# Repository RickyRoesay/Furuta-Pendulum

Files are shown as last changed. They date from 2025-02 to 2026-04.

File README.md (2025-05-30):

# Furuta-Pendulum
Rotary Inverse Pendulum that acts like a cool desktop toy.  This project is a work in progress.
Inspired by [Ben Katz.](https://build-its-inprogress.blogspot.com/search/label/Pendulum)

**Goals:**  
  * Cheap to make.  That means no $100 encoders or outsourced manufacturing.
  * (Relatively) Easy to manufacture and assemble.  Only 3D printed parts and off the shelf components. No metalworking lathes.
  * Must have a screen and buttons for a selectable mode of operation (swing up, swing down, etc).  *It's not feature creep, I swear!*
  * LED's that track the position and angle of the pendulum.  *Totally not feature creep!*
  * Project timeline should be less than a year.  Must use/adapt pre-existing software and hardware when possible. 

&nbsp;

**Proof of concept:**



&nbsp;

**Photos of CAD Assembly:**

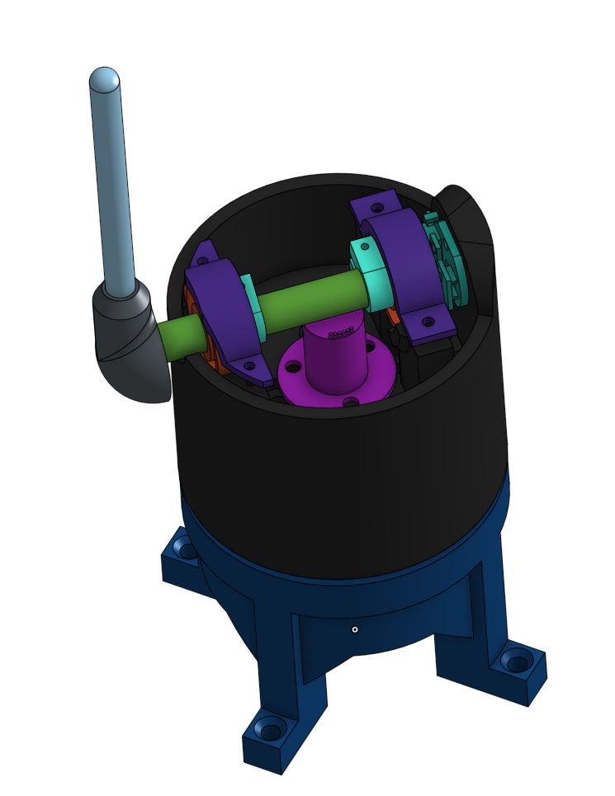
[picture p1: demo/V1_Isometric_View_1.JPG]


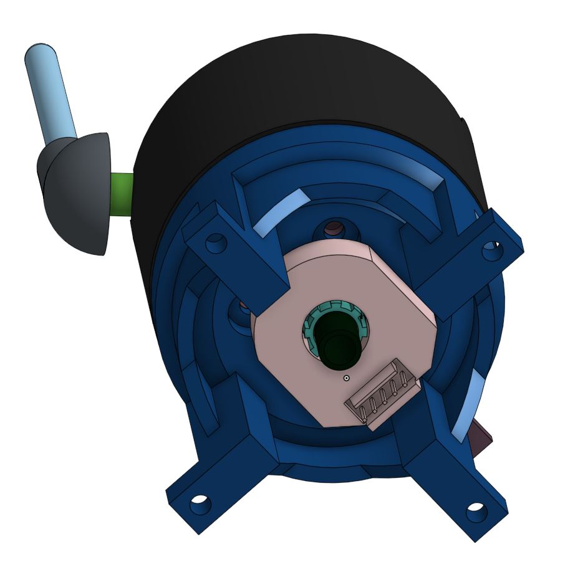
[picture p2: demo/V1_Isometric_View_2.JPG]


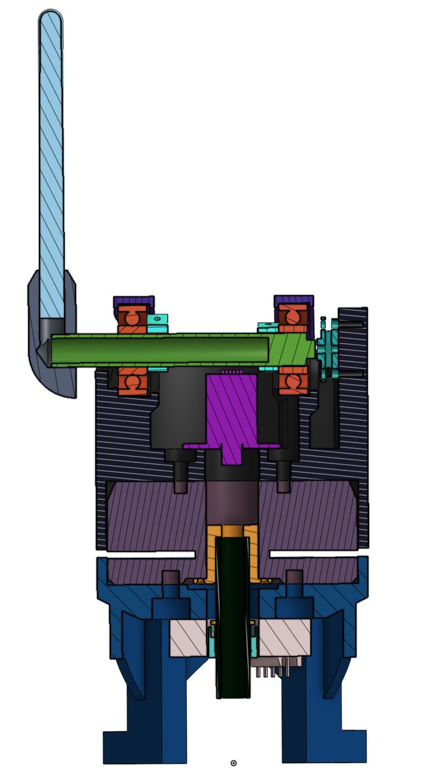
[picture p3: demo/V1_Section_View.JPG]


Link to the Onshape assembly can be found [here.](https://cad.onshape.com/documents/4a67b189595e38217c106822/w/59857a47126e04b0fa59ae61/e/db35a9295bf508af3468f325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)

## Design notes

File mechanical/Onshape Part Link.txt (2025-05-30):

https://cad.onshape.com/documents/4a67b189595e38217c106822/w/59857a47126e04b0fa59ae61/e/db35a9295bf508af3468f325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

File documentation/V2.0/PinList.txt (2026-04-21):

AS5047_nCS  -> PB2                  GPIO config'd, not a slave select pin
AS5047_CLK  -> Aux1 A -> PA5        AF5, SPI1 SCLK
AS5047_MISO -> Aux1 B -> PB4        AF5, SPI1 MISO
AS5047_MOSI -> Aux1 C -> PA7        AF5, SPI1 MOSI
SSD1357__D#                     -> Aux1 E -> PB3 & PB9
SSD1357__nRST                   -> Aux1 D -> PA15
SSD1357__SCLK                   -> Aux2 A -> PF1                       AF5, SPI2 SCLK
SSD1357__MISO                   -> Aux2 B -> PF0 & PA10 (PA10 used)    AF5, SPI2 MISO
SSD1357__MOSI                   -> Aux2 C -> PC4 & PA11 (PA11 used)    AF5, SPI2 MOSI
SSD1357__nCS                    -> Aux2 D -> PB7                       
SPI3_SCLK
SPI3_MOSI
SPI3_MISO
IMU_nCS
IMU_INT1
IMU_INT2
DRV8323_nCS
DRV8323_nFAULT
DRV8323_ENABLE
EEPROM_nCS
EEPROM_nWP
PH_A_HS
PH_A_LS
PH_B_HS
PH_B_LS
PH_C_HS
PH_C_LS
PH_A_Isns
PH_B_Isns
PH_C_Isns
FET_NTC_Vsns
PRECHARGE_NTC_Vsns
VBUS_IN_Vsns
VBUS_Post_PC_Vsns
V5p0_Vsns
V3p3_Vsns
Motor_ENC_A
Motor_ENC_A
Motor_ENC_B
Motor_ENC_B
Motor_ENC_Z
Motor_ENC_Z
PRECHARGE_BYPASS_EN
LED 
SPARE_1
SPARE_2
DAC_1
DAC_2
WS2812B_Dout
Menu_ENC_A
Menu_ENC_B
Menu_ENC_Push_Btn
Soft_Key_Switch_Btn
CAN_TX
CAN_RX
OSC_XTAL_1
OSC_XTAL_2

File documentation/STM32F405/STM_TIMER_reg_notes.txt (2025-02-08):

TIMx_CCRx    capture compare reg

CK_CNT  prescaler output that's enabled with CEN  

TIMx_CR1  control register 1
	CKD clock division
	ARPE
	CMS center aligned mode selection
	DIR (up vs down counter) assuming center vs encoder mode isn't selected
	OPM one pulse mode
	URS  update request source, 0 = lots of events generate an update-interupt/DMA request, 1 = only counter-over/underflow generate an update interrupt/dma req
	UDIS  update disable, 0 = UEV enabled, 1 = uev disabled
	CEN counter enable bit 

CCXIF flag

auto-reload preload enable bit (ARPE), 0 = TIMx_ARR is not preloaded (immediated takes effect), if = 1, then TIMx_ARR change takes effect mid counter period

• Counter register (TIMx_CNT)
• Prescaler register (TIMx_PSC)  also prescale control register
• Auto-reload register (TIMx_ARR)
• Repetition counter register (TIMx_RCR)

TIMx_ARR  auto reload, tells counter to restart to 0 (upcounting), and generates a counter overflow event 

if the repetition counter is used, the update event (UEV) is generated upon over/underflow of TIMx_CNT

if URS bit (update request selection) in TIMx_CR1, 

12.4 tim1 regs, at pg 287

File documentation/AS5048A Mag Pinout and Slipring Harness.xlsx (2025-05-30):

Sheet: main
pads on the left, from top to bottom
Signal: | Wire Color:
gnd | black
csn | yellow
clk | green
mosi | white
miso | blue/ light blue
vdd5v | red
gnd
gnd
All Pinouts/wire connections
signal name | mag sensor | slip ring | slip ring "section" | odesc pigtail
miso | blue/ light blue | black | 1 | blue
 |  | yellow
clk | green | red |  | green
 |  | blue
mosi | white | grey |  | white
 |  | pink
vdd5v | red | orange | 2 | black
 |  | brown
csn | yellow | green |  | yellow
 |  | purple
gnd | black | white |  | red
 |  | light blue

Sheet: cheapo
pads on the left, negative terminal on top:
gnd
gnd
5V
MISO
MOSI
CLK
nCS
gnd

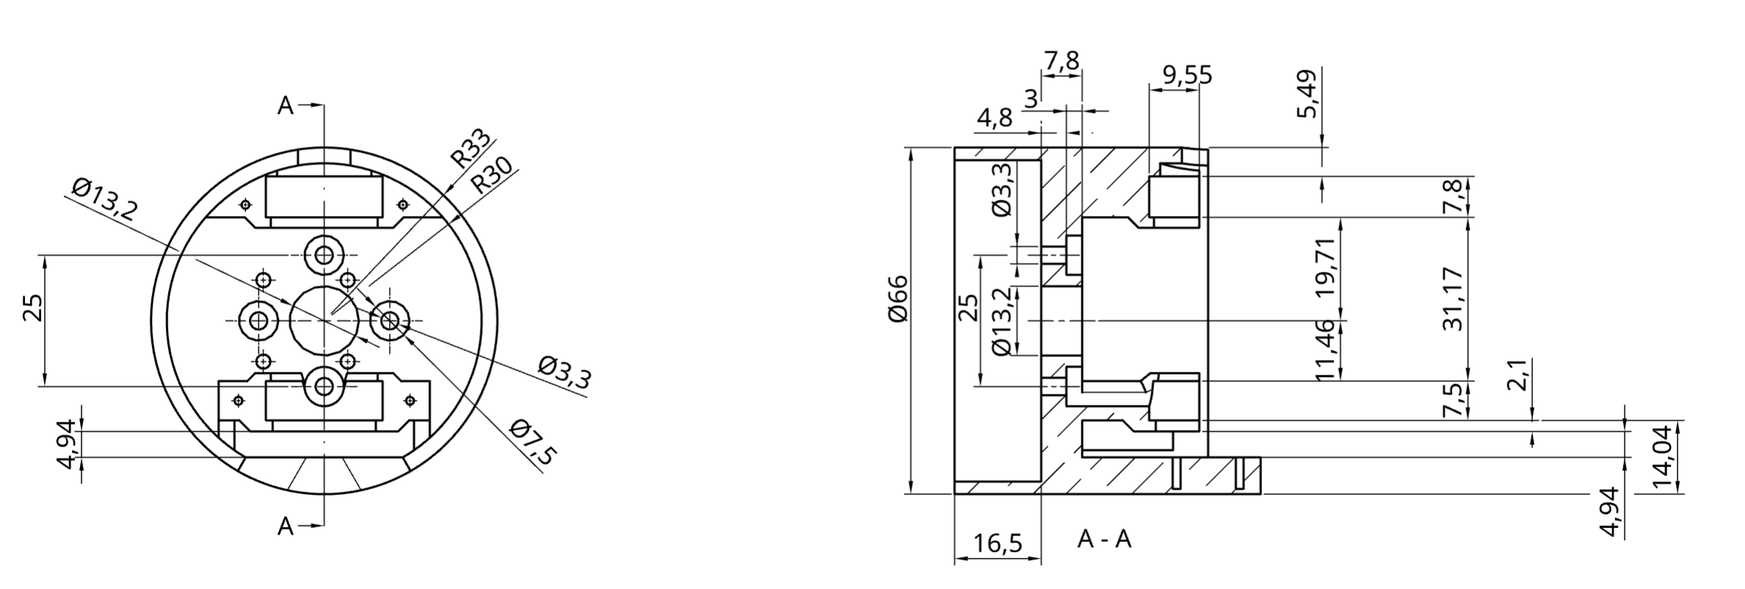
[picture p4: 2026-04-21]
mechanical/Top Rotor Pendulum Mount.png

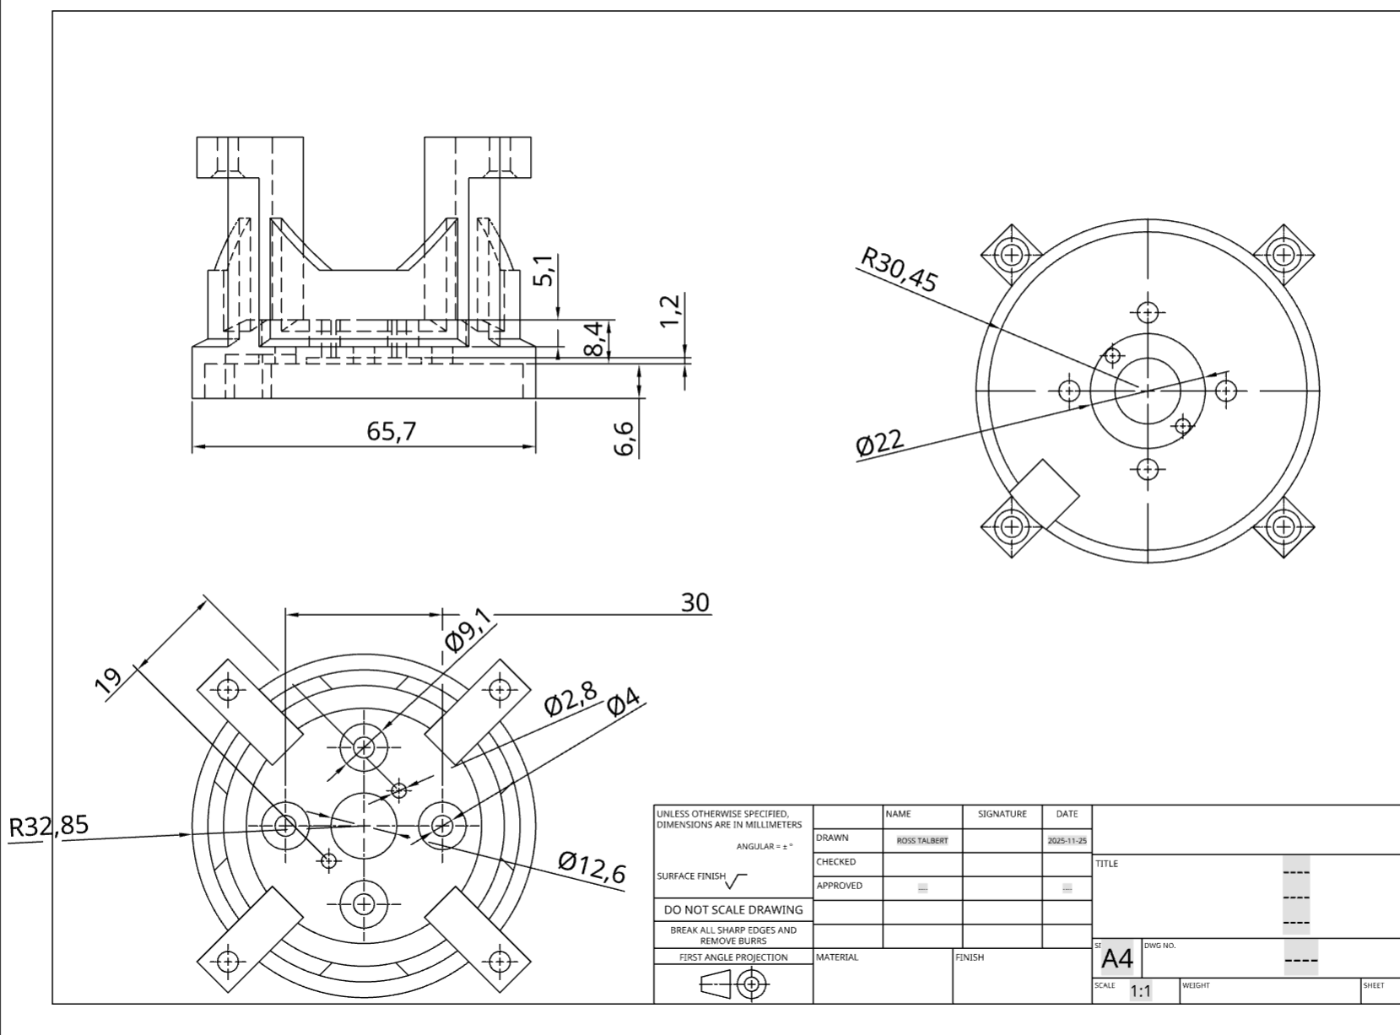
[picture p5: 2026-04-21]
mechanical/Bottom Motor Mount Drawing.png

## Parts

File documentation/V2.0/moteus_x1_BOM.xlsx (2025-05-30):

Reference | Value | Footprint | Do Not Place | Exclude from BOM | MF | MPN | quantity | Cost | Total Cost | asdf | asfd
L2 | 100uH | moteus:IND_6028-WE-LQS_WRE |  |  | Wurth Electronics | 74404063101 | 1 | 1.08 | 1.08
C24 | 0.1uF 100V | Capacitor_SMD:C_1812_4532Metric |  |  | KYOCERA AVX | 18121C104MAT2A | 3 | 0.49 | 1.47
D4 | BAT41KFILM | moteus:SOD-523_STM |  |  | ST | BAT41KFILM | 7 | 0.206 | 1.442
C22 | 47nF 100V | Capacitor_SMD:C_0603_1608Metric |  |  | KEMET | C0603X473K1RAC7867 | 1 | 0.266 | 0.266
C21 | 1uF 25V | Capacitor_SMD:C_0603_1608Metric |  |  | TDK | C1608X7R1E105K080AE | 2 | 0.138 | 0.276
C12 | 4.7uF | Capacitor_SMD:C_0603_1608Metric |  |  |  | CL10A475KP8NNNC | 1 | 0.01 | 0.01
L1 | 2.2uH | moteus:IND_DFE252012_MUR |  |  | MURATA | DFE252012PD-2R2M=P2 | 2 | 0.33 | 0.66
U5 | DRV8353SRTAR | moteus:RTA0040B |  |  | TI | DRV8353SRTAR | 1 | 4.42 | 4.42
Q1 | FDMT80080DC | Package_TO_SOT_SMD:PQFN_8x8 |  |  | ONSEMI | FDMT80080DC | 6 | 0.927 | 5.562
C2 | 0.1uF 100V | Capacitor_SMD:C_0603_1608Metric |  |  | MURATA | GCJ188R72A104KA01D | 2 | 0.1 | 0.2
C5 | 5600pF | Capacitor_SMD:C_0402_1005Metric |  |  | MURATA | GCM155R71E562KA37D | 1 | 0.02 | 0.02
C1 | 1uF 100V | Capacitor_SMD:C_0805_2012Metric |  |  | MURATA | GCM21BC72A105KE36L | 1 | 0.269 | 0.269
C45 | 4.7uF 100V | Capacitor_SMD:C_1206_3216Metric |  |  | MURATA | GRJ31CC72A475KE01K | 37 | 0.361 | 13.357
C4 | 22uF | Capacitor_SMD:C_1210_3225Metric |  |  | MURATA | GRM32ER71E226KE15L | 3 | 0.475 | 1.425
U7 | MA600 | Package_DFN_QFN:QFN-16-1EP_3x3mm_P0.5mm_EP1.75x1.75mm |  |  | MPS | MA600GQE-0000 | 0 |  | 0
U1 | MAX17760ATC+ | moteus:21-0664E_1233-1C_MXM |  |  | Analog | MAX17760ATC+ | 1 | 4.05 | 4.05
C11 | 0.1uF | Capacitor_SMD:C_0402_1005Metric |  |  |  | MF-CAP-0402-0.1uF | 12 |  | 0
C27 | 1000pF | Capacitor_SMD:C_0402_1005Metric |  |  |  | MF-CAP-0402-1nF | 3 |  | 0
C3 | 1uF | Capacitor_SMD:C_0402_1005Metric |  |  |  | MF-CAP-0402-1uF | 10 |  | 0
C10 | 10uF | Capacitor_SMD:C_1206_3216Metric |  |  |  | MF-CAP-1206-10uF | 1 |  | 0
D2 | LED | LED_SMD:LED_0603_1608Metric |  |  |  | MF-LED-0603-GREEN | 1 |  | 0
D1 | LED | LED_SMD:LED_0603_1608Metric |  |  |  | MF-LED-0603-RED | 1 |  | 0
R23 | 47k NTC | Resistor_SMD:R_0402_1005Metric |  |  | MURATA | NCP15WB473F03RC | 1 |  | 0
R7 | 16.2k 1% | Resistor_SMD:R_0402_1005Metric |  |  | YAGEO | RC0402FR-0716K2L | 1 |  | 0
R6 | 226k 1% | Resistor_SMD:R_0402_1005Metric |  |  | YAGEO | RC0402FR-07226KL | 1 |  | 0
R1 | 42.2k 1% | Resistor_SMD:R_0402_1005Metric |  |  | YAGEO | RC0402FR-0742K2L | 1 |  | 0
R5 | 52.3k 1% | Resistor_SMD:R_0402_1005Metric |  |  | YAGEO | RC0402FR-0752K3L | 1 |  | 0
R2 | 69.8k 1% | Resistor_SMD:R_0402_1005Metric |  |  | YAGEO | RC0402FR-0769K8L | 1 |  | 0
R3 | 80.6k 1% | Resistor_SMD:R_0402_1005Metric |  |  | YAGEO | RC0402FR-0780K6L | 1 |  | 0
CAN1 | S3B-PH-SM4-TB(LF)(SN) | moteus:JST_S3B-PH-SM4-TB(LF)(SN) |  |  | JST | S3B-PH-SM4-TB(LF)(SN) | 2 | 0.64 | 1.28
SWD1 | S6B-ZR-SM4A-TF(LF)(SN) | moteus:JST_S6B-ZR-SM4A-TF(LF)(SN) |  |  | JST | S6B-ZR-SM4A-TF(LF)(SN) | 1 | 0.421 | 0.421
J3 | SM06B-GHS-TB | moteus:CONN_SM06B-GHS-TB_JST |  |  | JST | SM06B-GHS-TB(LF)(SN) | 1 | 0.25 | 0.25
AUX2 | SM07B-GHS-TB(LF)(SN) | moteus:JST_SM07B-GHS-TB(LF)(SN) |  |  | JST | SM07B-GHS-TB(LF)(SN) | 1 | 0.606 | 0.606
AUX1 | SM08B-GHS-TB | moteus:CONN_SM08B-GHS-TB_JST |  |  | JST | SM08B-GHS-TB(LF)(SN) | 1 | 0.447 | 0.447
D3 | SMBJ51D-M3/I | Diode_SMD:D_SMB |  |  | VISHAY | SMBJ51D-M3/I | 1 | 0.36 | 0.36
U8 | SN65HVD35DR | moteus:D14 |  |  | TI | SN65HVD35DR | 0 | N/A
U4 | STM32G474CEU6 | moteus:UFQFPN-48_7X7X0P55MM |  |  | ST | STM32G474CEU6 | 1 | 7.9 | 7.9
D13 | US1B | Diode_SMD:D_SMA |  |  | ST | STPS1H100A | 1 | 0.34 | 0.34
U6 | TCAN1057AEV-Q1 | moteus:SOIC-8_3.9x4.9mm_P1.27mm |  |  | TI | TCAN1057AEVDRQ1 | 1 | 1.42 | 1.42
U2 | TPS629203DRLR | moteus:SOT-5x3_DRL0008A_TEX |  |  | TI | TPS629203DRLR | 2 | 0.86 | 1.72
R14 | 0.5mOhm | Resistor_SMD:R_2512_6332Metric |  |  | VISHAY DALE | WSLF2512L5000FEA | 3 | 0.91 | 2.73
 |  |  |  |  |  |  |  |  | 51.981

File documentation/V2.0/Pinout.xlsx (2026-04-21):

Position | Name | Type | Signal | Label | AF0 | AF1 | AF2 | AF3 | AF4 | AF5 | AF6 | AF7 | AF8 | AF9 | AF10 | AF11 | AF12 | AF13 | AF14 | AF15
1 | PE2 | I/O |  |  | SYS_TRACECLK |  | TIM3_CH1 | SAI1_CK1 |  | SPI4_SCK | TIM20_CH1 |  |  |  |  |  | FMC_A23 | SAI1_MCLK_A |  | EVENTOUT
2 | PE3 | I/O |  |  | SYS_TRACED0 |  | TIM3_CH2 |  |  | SPI4_NSS | TIM20_CH2 |  |  |  |  |  | FMC_A19 | SAI1_SD_B |  | EVENTOUT
3 | PE4 | I/O |  |  | SYS_TRACED1 |  | TIM3_CH3 | SAI1_D2 |  | SPI4_NSS | TIM20_CH1N |  |  |  |  |  | FMC_A20 | SAI1_FS_A |  | EVENTOUT
4 | PE5 | I/O |  |  | SYS_TRACED2 |  | TIM3_CH4 | SAI1_CK2 |  | SPI4_MISO | TIM20_CH2N |  |  |  |  |  | FMC_A21 | SAI1_SCK_A |  | EVENTOUT
5 | PE6 | I/O |  |  | SYS_TRACED3 |  |  | SAI1_D1 |  | SPI4_MOSI | TIM20_CH3N |  |  |  |  |  | FMC_A22 | SAI1_SD_A |  | EVENTOUT
6 | VBAT | Power
7 | PC13 | I/O |  |  |  |  | TIM1_BKIN |  | TIM1_CH1N |  | TIM8_CH4N |  |  |  |  |  |  |  |  | EVENTOUT
8 | PC14-OSC32_IN | I/O |  |  |  |  |  |  |  |  |  |  |  |  |  |  |  |  |  | EVENTOUT
9 | PC15-OSC32_OUT | I/O |  |  |  |  |  |  |  |  |  |  |  |  |  |  |  |  |  | EVENTOUT
10 | PF9 | I/O |  |  |  |  | TIM20_BKIN | TIM15_CH1 |  | SPI2_SCK | TIM5_CH4 |  |  |  | QUADSPI1_BK1_IO1 |  | FMC_A25 | SAI1_FS_B |  | EVENTOUT
11 | PF10 | I/O |  |  |  |  | TIM20_BKIN2 | TIM15_CH2 |  | SPI2_SCK |  |  |  |  | QUADSPI1_CLK |  | FMC_A0 | SAI1_D3 |  | EVENTOUT
12 | PF0-OSC_IN | I/O |  |  |  |  |  |  | I2C2_SDA | I2S2_WS/SPI2_NSS | TIM1_CH3N |  |  |  |  |  |  |  |  | EVENTOUT
13 | PF1-OSC_OUT | I/O |  |  |  |  |  |  |  | I2S2_CK/SPI2_SCK |  |  |  |  |  |  |  |  |  | EVENTOUT
14 | PG10-NRST | I/O |  |  | RCC_MCO |  |  |  |  |  |  |  |  |  |  |  |  |  |  | EVENTOUT
15 | PC0 | I/O |  |  |  | LPTIM1_IN1 | TIM1_CH1 |  |  |  |  |  | LPUART1_RX |  |  |  |  |  |  | EVENTOUT
16 | PC1 | I/O |  |  |  | LPTIM1_OUT | TIM1_CH2 |  |  |  |  |  | LPUART1_TX |  | QUADSPI1_BK2_IO0 |  |  | SAI1_SD_A |  | EVENTOUT
17 | PC2 | I/O |  |  |  | LPTIM1_IN2 | TIM1_CH3 | COMP3_OUT |  |  | TIM20_CH2 |  |  |  | QUADSPI1_BK2_IO1 |  |  |  |  | EVENTOUT
18 | PC3 | I/O |  |  |  | LPTIM1_ETR | TIM1_CH4 | SAI1_D1 |  |  | TIM1_BKIN2 |  |  |  | QUADSPI1_BK2_IO2 |  |  | SAI1_SD_A |  | EVENTOUT
19 | PF2 | I/O |  |  |  |  | TIM20_CH3 |  | I2C2_SMBA |  |  |  |  |  |  |  | FMC_A2 |  |  | EVENTOUT
20 | PA0 | I/O |  |  |  | TIM2_CH1 | TIM5_CH1 |  |  |  |  | USART2_CTS/USART2_NSS | COMP1_OUT | TIM8_BKIN | TIM8_ETR |  |  |  | TIM2_ETR | EVENTOUT
21 | PA1 | I/O |  |  | RTC_REFIN | TIM2_CH2 | TIM5_CH2 |  |  |  |  | USART2_DE/USART2_RTS |  | TIM15_CH1N |  |  |  |  |  | EVENTOUT
22 | PA2 | I/O |  |  |  | TIM2_CH3 | TIM5_CH3 |  |  |  |  | USART2_TX | COMP2_OUT | TIM15_CH1 | QUADSPI1_BK1_NCS |  | LPUART1_TX |  | UCPD1_FRSTX1/UCPD1_FRSTX2 | EVENTOUT
23 | VSS | Power
24 | VDD | Power
25 | PA3 | I/O |  |  |  | TIM2_CH4 | TIM5_CH4 | SAI1_CK1 |  |  |  | USART2_RX |  | TIM15_CH2 | QUADSPI1_CLK |  | LPUART1_RX | SAI1_MCLK_A |  | EVENTOUT
26 | PA4 | I/O |  |  |  |  | TIM3_CH2 |  |  | SPI1_NSS | I2S3_WS/SPI3_NSS | USART2_CK |  |  |  |  |  | SAI1_FS_B |  | EVENTOUT
27 | PA5 | I/O |  |  |  | TIM2_CH1 | TIM2_ETR |  |  | SPI1_SCK |  |  |  |  |  |  |  |  | UCPD1_FRSTX1/UCPD1_FRSTX2 | EVENTOUT
28 | PA6 | I/O |  |  |  | TIM16_CH1 | TIM3_CH1 |  | TIM8_BKIN | SPI1_MISO | TIM1_BKIN |  | COMP1_OUT |  | QUADSPI1_BK1_IO3 |  | LPUART1_CTS |  |  | EVENTOUT
29 | PA7 | I/O |  |  |  | TIM17_CH1 | TIM3_CH2 |  | TIM8_CH1N | SPI1_MOSI | TIM1_CH1N |  | COMP2_OUT |  | QUADSPI1_BK1_IO2 |  |  |  | UCPD1_FRSTX1/UCPD1_FRSTX2 | EVENTOUT
30 | PC4 | I/O |  |  |  |  | TIM1_ETR |  | I2C2_SCL |  |  | USART1_TX |  |  | QUADSPI1_BK2_IO3 |  |  |  |  | EVENTOUT
31 | PC5 | I/O |  |  |  |  | TIM15_BKIN | SAI1_D3 |  |  | TIM1_CH4N | USART1_RX |  |  |  |  |  | HRTIM1_EEV10 |  | EVENTOUT
32 | PB0 | I/O |  |  |  |  | TIM3_CH3 |  | TIM8_CH2N |  | TIM1_CH2N |  |  |  | QUADSPI1_BK1_IO1 |  |  | HRTIM1_FLT5 | UCPD1_FRSTX1/UCPD1_FRSTX2 | EVENTOUT
33 | PB1 | I/O |  |  |  |  | TIM3_CH4 |  | TIM8_CH3N |  | TIM1_CH3N |  | COMP4_OUT |  | QUADSPI1_BK1_IO0 |  | LPUART1_DE/LPUART1_RTS | HRTIM1_SCOUT |  | EVENTOUT
34 | PB2 | I/O |  |  | RTC_OUT2 | LPTIM1_OUT | TIM5_CH1 | TIM20_CH1 | I2C3_SMBA |  |  |  |  |  | QUADSPI1_BK2_IO1 |  |  | HRTIM1_SCIN |  | EVENTOUT
35 | VSSA | Power
36 | VREF+ | MonoIO
37 | VDDA | Power
38 | PE7 | I/O |  |  |  |  | TIM1_ETR |  |  |  |  |  |  |  |  |  | FMC_D4/FMC_DA4 | SAI1_SD_B |  | EVENTOUT
39 | PE8 | I/O |  |  |  | TIM5_CH3 | TIM1_CH1N |  |  |  |  |  |  |  |  |  | FMC_D5/FMC_DA5 | SAI1_SCK_B |  | EVENTOUT
40 | PE9 | I/O |  |  |  | TIM5_CH4 | TIM1_CH1 |  |  |  |  |  |  |  |  |  | FMC_D6/FMC_DA6 | SAI1_FS_B |  | EVENTOUT
41 | PE10 | I/O |  |  |  |  | TIM1_CH2N |  |  |  |  |  |  |  | QUADSPI1_CLK |  | FMC_D7/FMC_DA7 | SAI1_MCLK_B |  | EVENTOUT
42 | PE11 | I/O |  |  |  |  | TIM1_CH2 |  |  | SPI4_NSS |  |  |  |  | QUADSPI1_BK1_NCS |  | FMC_D8/FMC_DA8 |  |  | EVENTOUT
43 | PE12 | I/O |  |  |  |  | TIM1_CH3N |  |  | SPI4_SCK |  |  |  |  | QUADSPI1_BK1_IO0 |  | FMC_D9/FMC_DA9 |  |  | EVENTOUT
44 | PE13 | I/O |  |  |  |  | TIM1_CH3 |  |  | SPI4_MISO |  |  |  |  | QUADSPI1_BK1_IO1 |  | FMC_D10/FMC_DA10 |  |  | EVENTOUT
45 | PE14 | I/O |  |  |  |  | TIM1_CH4 |  |  | SPI4_MOSI | TIM1_BKIN2 |  |  |  | QUADSPI1_BK1_IO2 |  | FMC_D11/FMC_DA11 |  |  | EVENTOUT
46 | PE15 | I/O |  |  |  |  | TIM1_BKIN |  |  |  | TIM1_CH4N | USART3_RX |  |  | QUADSPI1_BK1_IO3 |  | FMC_D12/FMC_DA12 |  |  | EVENTOUT
47 | PB10 | I/O |  |  |  | TIM2_CH3 |  |  |  |  |  | USART3_TX | LPUART1_RX |  | QUADSPI1_CLK |  | TIM1_BKIN | HRTIM1_FLT3 | SAI1_SCK_A | EVENTOUT
48 | VSS | Power
49 | VDD | Power
50 | PB11 | I/O |  |  |  | TIM2_CH4 |  |  |  |  |  | USART3_RX | LPUART1_TX |  | QUADSPI1_BK1_NCS |  |  | HRTIM1_FLT4 |  | EVENTOUT
51 | PB12 | I/O |  |  |  |  | TIM5_ETR |  | I2C2_SMBA | I2S2_WS/SPI2_NSS | TIM1_BKIN | USART3_CK | LPUART1_DE/LPUART1_RTS | FDCAN2_RX |  |  |  | HRTIM1_CHC1 |  | EVENTOUT
52 | PB13 | I/O |  |  |  |  |  |  |  | I2S2_CK/SPI2_SCK | TIM1_CH1N | USART3_CTS/USART3_NSS | LPUART1_CTS | FDCAN2_TX |  |  |  | HRTIM1_CHC2 |  | EVENTOUT
53 | PB14 | I/O |  |  |  | TIM15_CH1 |  |  |  | SPI2_MISO | TIM1_CH2N | USART3_DE/USART3_RTS | COMP4_OUT |  |  |  |  | HRTIM1_CHD1 |  | EVENTOUT
54 | PB15 | I/O |  |  | RTC_REFIN | TIM15_CH2 | TIM15_CH1N | COMP3_OUT | TIM1_CH3N | I2S2_SD/SPI2_MOSI |  |  |  |  |  |  |  | HRTIM1_CHD2 |  | EVENTOUT
55 | PD8 | I/O |  |  |  |  |  |  |  |  |  | USART3_TX |  |  |  |  | FMC_D13/FMC_DA13 |  |  | EVENTOUT
56 | PD9 | I/O |  |  |  |  |  |  |  |  |  | USART3_RX |  |  |  |  | FMC_D14/FMC_DA14 |  |  | EVENTOUT
57 | PD10 | I/O |  |  |  |  |  |  |  |  |  | USART3_CK |  |  |  |  | FMC_D15/FMC_DA15 |  |  | EVENTOUT
58 | PD11 | I/O |  |  |  | TIM5_ETR |  |  | I2C4_SMBA |  |  | USART3_CTS/USART3_NSS |  |  |  |  | FMC_A16 |  |  | EVENTOUT
59 | PD12 | I/O |  |  |  |  | TIM4_CH1 |  |  |  |  | USART3_DE/USART3_RTS |  |  |  |  | FMC_A17 |  |  | EVENTOUT
60 | PD13 | I/O |  |  |  |  | TIM4_CH2 |  |  |  |  |  |  |  |  |  | FMC_A18 |  |  | EVENTOUT
61 | PD14 | I/O |  |  |  |  | TIM4_CH3 |  |  |  |  |  |  |  |  |  | FMC_D0/FMC_DA0 |  |  | EVENTOUT
62 | PD15 | I/O |  |  |  |  | TIM4_CH4 |  |  |  | SPI2_NSS |  |  |  |  |  | FMC_D1/FMC_DA1 |  |  | EVENTOUT
63 | VSS | Power
64 | VDD | Power
65 | PC6 | I/O |  |  |  |  | TIM3_CH1 | HRTIM1_EEV10 | TIM8_CH1 |  | I2S2_MCK | COMP6_OUT | I2C4_SCL |  |  |  |  | HRTIM1_CHF1 |  | EVENTOUT
66 | PC7 | I/O |  |  |  |  | TIM3_CH2 | HRTIM1_FLT5 | TIM8_CH2 |  | I2S3_MCK | COMP5_OUT | I2C4_SDA |  |  |  |  | HRTIM1_CHF2 |  | EVENTOUT
67 | PC8 | I/O |  |  |  |  | TIM3_CH3 | HRTIM1_CHE1 | TIM8_CH3 |  | TIM20_CH3 | COMP7_OUT | I2C3_SCL |  |  |  |  |  |  | EVENTOUT
68 | PC9 | I/O |  |  |  |  | TIM3_CH4 | HRTIM1_CHE2 | TIM8_CH4 | I2S_CKIN | TIM8_BKIN2 |  | I2C3_SDA |  |  |  |  |  |  | EVENTOUT
69 | PA8 | I/O |  |  | RCC_MCO |  | I2C3_SCL |  | I2C2_SDA | I2S2_MCK | TIM1_CH1 | USART1_CK | COMP7_OUT |  | TIM4_ETR | FDCAN3_RX | SAI1_CK2 | HRTIM1_CHA1 | SAI1_SCK_A | EVENTOUT
70 | PA9 | I/O |  |  |  |  | I2C3_SMBA |  | I2C2_SCL | I2S3_MCK | TIM1_CH2 | USART1_TX | COMP5_OUT | TIM15_BKIN | TIM2_CH3 |  |  | HRTIM1_CHA2 | SAI1_FS_A | EVENTOUT
71 | PA10 | I/O |  |  |  | TIM17_BKIN |  | CRS_SYNC | I2C2_SMBA | SPI2_MISO | TIM1_CH3 | USART1_RX | COMP6_OUT |  | TIM2_CH4 | TIM8_BKIN | SAI1_D1 | HRTIM1_CHB1 | SAI1_SD_A | EVENTOUT
72 | PA11 | I/O |  |  |  |  |  |  |  | I2S2_SD/SPI2_MOSI | TIM1_CH1N | USART1_CTS/USART1_NSS | COMP1_OUT | FDCAN1_RX | TIM4_CH1 | TIM1_CH4 | TIM1_BKIN2 | HRTIM1_CHB2 |  | EVENTOUT
73 | PA12 | I/O |  |  |  | TIM16_CH1 |  |  |  | I2S_CKIN | TIM1_CH2N | USART1_DE/USART1_RTS | COMP2_OUT | FDCAN1_TX | TIM4_CH2 | TIM1_ETR |  | HRTIM1_FLT1 |  | EVENTOUT
74 | VSS | Power
75 | VDD | Power
76 | PA13 | I/O |  |  | SYS_JTMS-SWDIO | TIM16_CH1N |  | I2C4_SCL | I2C1_SCL | IR_OUT |  | USART3_CTS/USART3_NSS |  |  | TIM4_CH3 |  |  | SAI1_SD_B |  | EVENTOUT
77 | PA14 | I/O |  |  | SYS_JTCK-SWCLK | LPTIM1_OUT |  | I2C4_SMBA | I2C1_SDA | TIM8_CH2 | TIM1_BKIN | USART2_TX |  |  |  |  |  | SAI1_FS_B |  | EVENTOUT
78 | PA15 | I/O |  |  | SYS_JTDI | TIM2_CH1 | TIM8_CH1 |  | I2C1_SCL | SPI1_NSS | I2S3_WS/SPI3_NSS | USART2_RX | UART4_DE/UART4_RTS | TIM1_BKIN |  | FDCAN3_TX |  | HRTIM1_FLT2 | TIM2_ETR | EVENTOUT
79 | PC10 | I/O |  |  |  |  |  |  | TIM8_CH1N | UART4_TX | I2S3_CK/SPI3_SCK | USART3_TX |  |  |  |  |  | HRTIM1_FLT6 |  | EVENTOUT
80 | PC11 | I/O |  |  |  |  |  | HRTIM1_EEV2 | TIM8_CH2N | UART4_RX | SPI3_MISO | USART3_RX | I2C3_SDA |  |  |  |  |  |  | EVENTOUT
81 | PC12 | I/O |  |  |  | TIM5_CH2 |  | HRTIM1_EEV1 | TIM8_CH3N | UART5_TX | I2S3_SD/SPI3_MOSI | USART3_CK |  |  |  |  |  |  | UCPD1_FRSTX1/UCPD1_FRSTX2 | EVENTOUT
82 | PD0 | I/O |  |  |  |  |  |  |  |  | TIM8_CH4N |  |  | FDCAN1_RX |  |  | FMC_D2/FMC_DA2 |  |  | EVENTOUT
83 | PD1 | I/O |  |  |  |  |  |  | TIM8_CH4 |  | TIM8_BKIN2 |  |  | FDCAN1_TX |  |  | FMC_D3/FMC_DA3 |  |  | EVENTOUT
84 | PD2 | I/O |  |  |  |  | TIM3_ETR |  | TIM8_BKIN | UART5_RX |  |  |  |  |  |  |  |  |  | EVENTOUT
85 | PD3 | I/O |  |  |  |  | TIM2_CH1/TIM2_ETR |  |  |  |  | USART2_CTS/USART2_NSS |  |  | QUADSPI1_BK2_NCS |  | FMC_CLK |  |  | EVENTOUT
86 | PD4 | I/O |  |  |  |  | TIM2_CH2 |  |  |  |  | USART2_DE/USART2_RTS |  |  | QUADSPI1_BK2_IO0 |  | FMC_NOE |  |  | EVENTOUT
87 | PD5 | I/O |  |  |  |  |  |  |  |  |  | USART2_TX |  |  | QUADSPI1_BK2_IO1 |  | FMC_NWE |  |  | EVENTOUT
88 | PD6 | I/O |  |  |  |  | TIM2_CH4 | SAI1_D1 |  |  |  | USART2_RX |  |  | QUADSPI1_BK2_IO2 |  | FMC_NWAIT | SAI1_SD_A |  | EVENTOUT
89 | PD7 | I/O |  |  |  |  | TIM2_CH3 |  |  |  |  | USART2_CK |  |  | QUADSPI1_BK2_IO3 |  | FMC_NCE/FMC_NE1 |  |  | EVENTOUT
90 | PB3 | I/O |  |  | SYS_JTDO-SWO | TIM2_CH2 | TIM4_ETR | CRS_SYNC | TIM8_CH1N | SPI1_SCK | I2S3_CK/SPI3_SCK | USART2_TX |  |  | TIM3_ETR | FDCAN3_RX | HRTIM1_SCOUT | HRTIM1_EEV9 | SAI1_SCK_B | EVENTOUT
91 | PB4 | I/O |  |  | SYS_JTRST | TIM16_CH1 | TIM3_CH1 |  | TIM8_CH2N | SPI1_MISO | SPI3_MISO | USART2_RX | UART5_DE/UART5_RTS |  | TIM17_BKIN | FDCAN3_TX |  | HRTIM1_EEV7 | SAI1_MCLK_B | EVENTOUT
92 | PB5 | I/O |  |  |  | TIM16_BKIN | TIM3_CH2 | TIM8_CH3N | I2C1_SMBA | SPI1_MOSI | I2S3_SD/SPI3_MOSI | USART2_CK | I2C3_SDA | FDCAN2_RX | TIM17_CH1 | LPTIM1_IN1 | SAI1_SD_B | HRTIM1_EEV6 | UART5_CTS | EVENTOUT
93 | PB6 | I/O |  |  |  | TIM16_CH1N | TIM4_CH1 |  |  | TIM8_CH1 | TIM8_ETR | USART1_TX | COMP4_OUT | FDCAN2_TX | TIM8_BKIN2 | LPTIM1_ETR | HRTIM1_SCIN | HRTIM1_EEV4 | SAI1_FS_B | EVENTOUT
94 | PB7 | I/O |  |  |  | TIM17_CH1N | TIM4_CH2 | I2C4_SDA | I2C1_SDA | TIM8_BKIN |  | USART1_RX | COMP3_OUT |  | TIM3_CH4 | LPTIM1_IN2 | FMC_NL | HRTIM1_EEV3 | UART4_CTS | EVENTOUT
95 | PB8-BOOT0 | I/O |  |  |  | TIM16_CH1 | TIM4_CH3 | SAI1_CK1 | I2C1_SCL |  |  | USART3_RX | COMP1_OUT | FDCAN1_RX | TIM8_CH2 |  | TIM1_BKIN | HRTIM1_EEV8 | SAI1_MCLK_A | EVENTOUT
96 | PB9 | I/O |  |  |  | TIM17_CH1 | TIM4_CH4 | SAI1_D2 | I2C1_SDA |  | IR_OUT | USART3_TX | COMP2_OUT | FDCAN1_TX | TIM8_CH3 |  | TIM1_CH3N | HRTIM1_EEV5 | SAI1_FS_A | EVENTOUT
97 | PE0 | I/O |  |  |  |  | TIM4_ETR | TIM20_CH4N | TIM16_CH1 |  | TIM20_ETR | USART1_TX |  |  |  |  | FMC_NBL0 |  |  | EVENTOUT
98 | PE1 | I/O |  |  |  |  |  |  | TIM17_CH1 |  | TIM20_CH4 | USART1_RX |  |  |  |  | FMC_NBL1 |  |  | EVENTOUT
99 | VSS | Power
100 | VDD | Power

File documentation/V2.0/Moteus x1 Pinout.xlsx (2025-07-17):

Position | Name | Type | Signal | Label | AF0 | AF1 | AF2 | AF3 | AF4 | AF5 | AF6 | AF7 | AF8 | AF9 | AF10 | AF11 | AF12 | AF13 | AF14 | AF15 | Schematic Net Name | Notes
8 | PA0 | I/O |  |  |  | TIM2_CH1 | TIM5_CH1 |  |  |  |  | USART2_CTS/USART2_NSS | COMP1_OUT | TIM8_BKIN | TIM8_ETR |  |  |  | TIM2_ETR | EVENTOUT | MOTOR1
9 | PA1 | I/O |  |  | RTC_REFIN | TIM2_CH2 | TIM5_CH2 |  |  |  |  | USART2_DE/USART2_RTS |  | TIM15_CH1N |  |  |  |  |  | EVENTOUT | MOTOR2
32 | PA10 | I/O |  |  |  | TIM17_BKIN |  | CRS_SYNC | I2C2_SMBA | SPI2_MISO | TIM1_CH3 | USART1_RX | COMP6_OUT |  | TIM2_CH4 | TIM8_BKIN | SAI1_D1 | HRTIM1_CHB1 | SAI1_SD_A | EVENTOUT | AUX2_B
33 | PA11 | I/O |  |  |  |  |  |  |  | I2S2_SD/SPI2_MOSI | TIM1_CH1N | USART1_CTS/USART1_NSS | COMP1_OUT | FDCAN1_RX | TIM4_CH1 | TIM1_CH4 | TIM1_BKIN2 | HRTIM1_CHB2 |  | EVENTOUT | AUX2_C
34 | PA12 | I/O |  |  |  | TIM16_CH1 |  |  |  | I2S_CKIN | TIM1_CH2N | USART1_DE/USART1_RTS | COMP2_OUT | FDCAN1_TX | TIM4_CH2 | TIM1_ETR |  | HRTIM1_FLT1 |  | EVENTOUT | AUX2_I2C_PULLUP
37 | PA13 | I/O |  |  | SYS_JTMS-SWDIO | TIM16_CH1N |  | I2C4_SCL | I2C1_SCL | IR_OUT |  | USART3_CTS/USART3_NSS |  |  | TIM4_CH3 |  |  | SAI1_SD_B |  | EVENTOUT | SWDIO
38 | PA14 | I/O |  |  | SYS_JTCK-SWCLK | LPTIM1_OUT |  | I2C4_SMBA | I2C1_SDA | TIM8_CH2 | TIM1_BKIN | USART2_TX |  |  |  |  |  | SAI1_FS_B |  | EVENTOUT | SWCLK
39 | PA15 | I/O |  |  | SYS_JTDI | TIM2_CH1 | TIM8_CH1 |  | I2C1_SCL | SPI1_NSS | I2S3_WS/SPI3_NSS | USART2_RX |  | TIM1_BKIN |  | FDCAN3_TX |  | HRTIM1_FLT2 | TIM2_ETR | EVENTOUT | AUX1_D
10 | PA2 | I/O |  |  |  | TIM2_CH3 | TIM5_CH3 |  |  |  |  | USART2_TX | COMP2_OUT | TIM15_CH1 | QUADSPI1_BK1_NCS |  | LPUART1_TX |  | UCPD1_FRSTX1/UCPD1_FRSTX2 | EVENTOUT | MOTOR3
11 | PA3 | I/O |  |  |  | TIM2_CH4 | TIM5_CH4 | SAI1_CK1 |  |  |  | USART2_RX |  | TIM15_CH2 | QUADSPI1_CLK |  | LPUART1_RX | SAI1_MCLK_A |  | EVENTOUT | FCUR1
12 | PA4 | I/O |  |  |  |  | TIM3_CH2 |  |  | SPI1_NSS | I2S3_WS/SPI3_NSS | USART2_CK |  |  |  |  |  | SAI1_FS_B |  | EVENTOUT | DAC
13 | PA5 | I/O |  |  |  | TIM2_CH1 | TIM2_ETR |  |  | SPI1_SCK |  |  |  |  |  |  |  |  | UCPD1_FRSTX1/UCPD1_FRSTX2 | EVENTOUT | AUX1_A
14 | PA6 | I/O |  |  |  | TIM16_CH1 | TIM3_CH1 |  | TIM8_BKIN | SPI1_MISO | TIM1_BKIN |  | COMP1_OUT |  | QUADSPI1_BK1_IO3 |  | LPUART1_CTS |  |  | EVENTOUT | FCUR2
15 | PA7 | I/O |  |  |  | TIM17_CH1 | TIM3_CH2 |  | TIM8_CH1N | SPI1_MOSI | TIM1_CH1N |  | COMP2_OUT |  | QUADSPI1_BK1_IO2 |  |  |  | UCPD1_FRSTX1/UCPD1_FRSTX2 | EVENTOUT | AUX1_C
30 | PA8 | I/O |  |  | RCC_MCO |  | I2C3_SCL |  | I2C2_SDA | I2S2_MCK | TIM1_CH1 | USART1_CK | COMP7_OUT |  | TIM4_ETR | FDCAN3_RX | SAI1_CK2 | HRTIM1_CHA1 | SAI1_SCK_A | EVENTOUT | VTEMP_MOT
31 | PA9 | I/O |  |  |  |  | I2C3_SMBA |  | I2C2_SCL | I2S3_MCK | TIM1_CH2 | USART1_TX | COMP5_OUT | TIM15_BKIN | TIM2_CH3 |  |  | HRTIM1_CHA2 | SAI1_FS_A | EVENTOUT | VBAT_SENSE
16 | PB0 | I/O |  |  |  |  | TIM3_CH3 |  | TIM8_CH2N |  | TIM1_CH2N |  |  |  | QUADSPI1_BK1_IO1 |  |  | HRTIM1_FLT5 | UCPD1_FRSTX1/UCPD1_FRSTX2 | EVENTOUT | DRV8323_CS
17 | PB1 | I/O |  |  |  |  | TIM3_CH4 |  | TIM8_CH3N |  | TIM1_CH3N |  | COMP4_OUT |  | QUADSPI1_BK1_IO0 |  | LPUART1_DE/LPUART1_RTS | HRTIM1_SCOUT |  | EVENTOUT | FCUR3
22 | PB10 | I/O |  |  |  | TIM2_CH3 |  |  |  |  |  | USART3_TX | LPUART1_RX |  | QUADSPI1_CLK |  | TIM1_BKIN | HRTIM1_FLT3 | SAI1_SCK_A | EVENTOUT | RS422_RE
25 | PB11 | I/O |  |  |  | TIM2_CH4 |  |  |  |  |  | USART3_RX | LPUART1_TX |  | QUADSPI1_BK1_NCS |  |  | HRTIM1_FLT4 |  | EVENTOUT | RS422_DE
26 | PB12 | I/O |  |  |  |  | TIM5_ETR |  | I2C2_SMBA | I2S2_WS/SPI2_NSS | TIM1_BKIN | USART3_CK | LPUART1_DE/LPUART1_RTS | FDCAN2_RX |  |  |  | HRTIM1_CHC1 |  | EVENTOUT | VTEMP_FET
27 | PB13 | I/O |  |  |  |  |  |  |  | I2S2_CK/SPI2_SCK | TIM1_CH1N | USART3_CTS/USART3_NSS | LPUART1_CTS | FDCAN2_TX |  |  |  | HRTIM1_CHC2 |  | EVENTOUT | MOTOR_FAULT
28 | PB14 | I/O |  |  |  | TIM15_CH1 |  |  |  | SPI2_MISO | TIM1_CH2N | USART3_DE/USART3_RTS | COMP4_OUT |  |  |  |  | HRTIM1_CHD1 |  | EVENTOUT | AUX1_A
29 | PB15 | I/O |  |  | RTC_REFIN | TIM15_CH2 | TIM15_CH1N | COMP3_OUT | TIM1_CH3N | I2S2_SD/SPI2_MOSI |  |  |  |  |  |  |  | HRTIM1_CHD2 |  | EVENTOUT | LED1
18 | PB2 | I/O |  |  | RTC_OUT2 | LPTIM1_OUT | TIM5_CH1 | TIM20_CH1 | I2C3_SMBA |  |  |  |  |  | QUADSPI1_BK2_IO1 |  |  | HRTIM1_SCIN |  | EVENTOUT | AS5047_CS
40 | PB3 | I/O |  |  | SYS_JTDO-SWO | TIM2_CH2 | TIM4_ETR | CRS_SYNC | TIM8_CH1N | SPI1_SCK | I2S3_CK/SPI3_SCK | USART2_TX |  |  | TIM3_ETR | FDCAN3_RX | HRTIM1_SCOUT | HRTIM1_EEV9 | SAI1_SCK_B | EVENTOUT | AUX1_E
41 | PB4 | I/O |  |  | SYS_JTRST | TIM16_CH1 | TIM3_CH1 |  | TIM8_CH2N | SPI1_MISO | SPI3_MISO | USART2_RX |  |  | TIM17_BKIN | FDCAN3_TX |  | HRTIM1_EEV7 | SAI1_MCLK_B | EVENTOUT | AUX1_B
42 | PB5 | I/O |  |  |  | TIM16_BKIN | TIM3_CH2 | TIM8_CH3N | I2C1_SMBA | SPI1_MOSI | I2S3_SD/SPI3_MOSI | USART2_CK | I2C3_SDA | FDCAN2_RX | TIM17_CH1 | LPTIM1_IN1 | SAI1_SD_B | HRTIM1_EEV6 |  | EVENTOUT | CAN_RX
43 | PB6 | I/O |  |  |  | TIM16_CH1N | TIM4_CH1 |  |  | TIM8_CH1 | TIM8_ETR | USART1_TX | COMP4_OUT | FDCAN2_TX | TIM8_BKIN2 | LPTIM1_ETR | HRTIM1_SCIN | HRTIM1_EEV4 | SAI1_FS_B | EVENTOUT | CAN_TX
44 | PB7 | I/O |  |  |  | TIM17_CH1N | TIM4_CH2 | I2C4_SDA | I2C1_SDA | TIM8_BKIN |  | USART1_RX | COMP3_OUT |  | TIM3_CH4 | LPTIM1_IN2 |  | HRTIM1_EEV3 |  | EVENTOUT | AUX2_D
45 | PB8-BOOT0 | I/O |  |  |  | TIM16_CH1 | TIM4_CH3 | SAI1_CK1 | I2C1_SCL |  |  | USART3_RX | COMP1_OUT | FDCAN1_RX | TIM8_CH2 |  | TIM1_BKIN | HRTIM1_EEV8 | SAI1_MCLK_A | EVENTOUT | AUX1_I2C_PULLUP
46 | PB9 | I/O |  |  |  | TIM17_CH1 | TIM4_CH4 | SAI1_D2 | I2C1_SDA |  | IR_OUT | USART3_TX | COMP2_OUT | FDCAN1_TX | TIM8_CH3 |  | TIM1_CH3N | HRTIM1_EEV5 | SAI1_FS_A | EVENTOUT | AUX1_E
2 | PC13 | I/O |  |  |  |  | TIM1_BKIN |  | TIM1_CH1N |  | TIM8_CH4N |  |  |  |  |  |  |  |  | EVENTOUT | DRV8323_MOSI
3 | PC14-OSC32_IN | I/O |  |  |  |  |  |  |  |  |  |  |  |  |  |  |  |  |  | EVENTOUT | MOTOR_ENABLE
4 | PC15-OSC32_OUT | I/O |  |  |  |  |  |  |  |  |  |  |  |  |  |  |  |  |  | EVENTOUT | MOTOR_HIZ
5 | PF0-OSC_IN | I/O |  |  |  |  |  |  | I2C2_SDA | I2S2_WS/SPI2_NSS | TIM1_CH3N |  |  |  |  |  |  |  |  | EVENTOUT | AUX2_B
6 | PF1-OSC_OUT | I/O |  |  |  |  |  |  |  | I2S2_CK/SPI2_SCK |  |  |  |  |  |  |  |  |  | EVENTOUT | AUX2_A
7 | PG10-NRST | I/O |  |  | RCC_MCO |  |  |  |  |  |  |  |  |  |  |  |  |  |  | EVENTOUT | NRST
1 | VBAT | Power
24 | VDD | Power
36 | VDD | Power
48 | VDD | Power
21 | VDDA | Power
20 | VREF+ | MonoIO
23 | VSS | Power
35 | VSS | Power
47 | VSS | Power
19 | VSSA | Power

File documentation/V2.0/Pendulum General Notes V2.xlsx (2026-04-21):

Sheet: Pinout
Position | Name | Type | AF0 | AF1 | AF2 | AF3 | AF4 | AF5 | AF6 | AF7 | AF8 | AF9 | AF10 | AF11 | AF12 | AF13 | AF14 | AF15 | Schematic Net Name | Notes
1 | VBAT | Power
2 | PC13 | I/O |  |  | TIM1_BKIN |  | TIM1_CH1N |  | TIM8_CH4N |  |  |  |  |  |  |  |  | EVENTOUT
3 | PC14-OSC32_IN | I/O |  |  |  |  |  |  |  |  |  |  |  |  |  |  |  | EVENTOUT
4 | PC15-OSC32_OUT | I/O |  |  |  |  |  |  |  |  |  |  |  |  |  |  |  | EVENTOUT
5 | PF0-OSC_IN | I/O |  |  |  |  | I2C2_SDA | I2S2_WS/SPI2_NSS | TIM1_CH3N |  |  |  |  |  |  |  |  | EVENTOUT
6 | PF1-OSC_OUT | I/O |  |  |  |  |  | I2S2_CK/SPI2_SCK |  |  |  |  |  |  |  |  |  | EVENTOUT
7 | PG10-NRST | I/O | RCC_MCO |  |  |  |  |  |  |  |  |  |  |  |  |  |  | EVENTOUT
8 | PC0 | I/O |  | LPTIM1_IN1 | TIM1_CH1 |  |  |  |  |  | LPUART1_RX |  |  |  |  |  |  | EVENTOUT
9 | PC1 | I/O |  | LPTIM1_OUT | TIM1_CH2 |  |  |  |  |  | LPUART1_TX |  | QUADSPI1_BK2_IO0 |  |  | SAI1_SD_A |  | EVENTOUT
10 | PC2 | I/O |  | LPTIM1_IN2 | TIM1_CH3 | COMP3_OUT |  |  | TIM20_CH2 |  |  |  | QUADSPI1_BK2_IO1 |  |  |  |  | EVENTOUT
11 | PC3 | I/O |  | LPTIM1_ETR | TIM1_CH4 | SAI1_D1 |  |  | TIM1_BKIN2 |  |  |  | QUADSPI1_BK2_IO2 |  |  | SAI1_SD_A |  | EVENTOUT
12 | PA0 | I/O |  | TIM2_CH1 | TIM5_CH1 |  |  |  |  | USART2_CTS/USART2_NSS | COMP1_OUT | TIM8_BKIN | TIM8_ETR |  |  |  | TIM2_ETR | EVENTOUT
13 | PA1 | I/O | RTC_REFIN | TIM2_CH2 | TIM5_CH2 |  |  |  |  | USART2_DE/USART2_RTS |  | TIM15_CH1N |  |  |  |  |  | EVENTOUT
14 | PA2 | I/O |  | TIM2_CH3 | TIM5_CH3 |  |  |  |  | USART2_TX | COMP2_OUT | TIM15_CH1 | QUADSPI1_BK1_NCS |  | LPUART1_TX |  | UCPD1_FRSTX1/UCPD1_FRSTX2 | EVENTOUT
15 | VSS | Power
16 | VDD | Power
17 | PA3 | I/O |  | TIM2_CH4 | TIM5_CH4 | SAI1_CK1 |  |  |  | USART2_RX |  | TIM15_CH2 | QUADSPI1_CLK |  | LPUART1_RX | SAI1_MCLK_A |  | EVENTOUT
18 | PA4 | I/O |  |  | TIM3_CH2 |  |  | SPI1_NSS | I2S3_WS/SPI3_NSS | USART2_CK |  |  |  |  |  | SAI1_FS_B |  | EVENTOUT
19 | PA5 | Output |  | TIM2_CH1 | TIM2_ETR |  |  | SPI1_SCK |  |  |  |  |  |  |  |  | UCPD1_FRSTX1/UCPD1_FRSTX2 | EVENTOUT
20 | PA6 | I/O |  | TIM16_CH1 | TIM3_CH1 |  | TIM8_BKIN | SPI1_MISO | TIM1_BKIN |  | COMP1_OUT |  | QUADSPI1_BK1_IO3 |  | LPUART1_CTS |  |  | EVENTOUT
21 | PA7 | I/O |  | TIM17_CH1 | TIM3_CH2 |  | TIM8_CH1N | SPI1_MOSI | TIM1_CH1N |  | COMP2_OUT |  | QUADSPI1_BK1_IO2 |  |  |  | UCPD1_FRSTX1/UCPD1_FRSTX2 | EVENTOUT
22 | PC4 | I/O |  |  | TIM1_ETR |  | I2C2_SCL |  |  | USART1_TX |  |  | QUADSPI1_BK2_IO3 |  |  |  |  | EVENTOUT
23 | PC5 | I/O |  |  | TIM15_BKIN | SAI1_D3 |  |  | TIM1_CH4N | USART1_RX |  |  |  |  |  | HRTIM1_EEV10 |  | EVENTOUT
24 | PB0 | I/O |  |  | TIM3_CH3 |  | TIM8_CH2N |  | TIM1_CH2N |  |  |  | QUADSPI1_BK1_IO1 |  |  | HRTIM1_FLT5 | UCPD1_FRSTX1/UCPD1_FRSTX2 | EVENTOUT
25 | PB1 | I/O |  |  | TIM3_CH4 |  | TIM8_CH3N |  | TIM1_CH3N |  | COMP4_OUT |  | QUADSPI1_BK1_IO0 |  | LPUART1_DE/LPUART1_RTS | HRTIM1_SCOUT |  | EVENTOUT
26 | PB2 | I/O | RTC_OUT2 | LPTIM1_OUT | TIM5_CH1 | TIM20_CH1 | I2C3_SMBA |  |  |  |  |  | QUADSPI1_BK2_IO1 |  |  | HRTIM1_SCIN |  | EVENTOUT
27 | VSSA | Power
28 | VREF+ | MonoIO
29 | VDDA | Power
30 | PB10 | I/O |  | TIM2_CH3 |  |  |  |  |  | USART3_TX | LPUART1_RX |  | QUADSPI1_CLK |  | TIM1_BKIN | HRTIM1_FLT3 | SAI1_SCK_A | EVENTOUT
31 | VSS | Power
32 | VDD | Power
33 | PB11 | I/O |  | TIM2_CH4 |  |  |  |  |  | USART3_RX | LPUART1_TX |  | QUADSPI1_BK1_NCS |  |  | HRTIM1_FLT4 |  | EVENTOUT
34 | PB12 | I/O |  |  | TIM5_ETR |  | I2C2_SMBA | I2S2_WS/SPI2_NSS | TIM1_BKIN | USART3_CK | LPUART1_DE/LPUART1_RTS | FDCAN2_RX |  |  |  | HRTIM1_CHC1 |  | EVENTOUT
35 | PB13 | I/O |  |  |  |  |  | I2S2_CK/SPI2_SCK | TIM1_CH1N | USART3_CTS/USART3_NSS | LPUART1_CTS | FDCAN2_TX |  |  |  | HRTIM1_CHC2 |  | EVENTOUT
36 | PB14 | I/O |  | TIM15_CH1 |  |  |  | SPI2_MISO | TIM1_CH2N | USART3_DE/USART3_RTS | COMP4_OUT |  |  |  |  | HRTIM1_CHD1 |  | EVENTOUT
37 | PB15 | I/O | RTC_REFIN | TIM15_CH2 | TIM15_CH1N | COMP3_OUT | TIM1_CH3N | I2S2_SD/SPI2_MOSI |  |  |  |  |  |  |  | HRTIM1_CHD2 |  | EVENTOUT
38 | PC6 | I/O |  |  | TIM3_CH1 | HRTIM1_EEV10 | TIM8_CH1 |  | I2S2_MCK | COMP6_OUT | I2C4_SCL |  |  |  |  | HRTIM1_CHF1 |  | EVENTOUT
39 | PC7 | I/O |  |  | TIM3_CH2 | HRTIM1_FLT5 | TIM8_CH2 |  | I2S3_MCK | COMP5_OUT | I2C4_SDA |  |  |  |  | HRTIM1_CHF2 |  | EVENTOUT
40 | PC8 | I/O |  |  | TIM3_CH3 | HRTIM1_CHE1 | TIM8_CH3 |  | TIM20_CH3 | COMP7_OUT | I2C3_SCL |  |  |  |  |  |  | EVENTOUT
41 | PC9 | I/O |  |  | TIM3_CH4 | HRTIM1_CHE2 | TIM8_CH4 | I2S_CKIN | TIM8_BKIN2 |  | I2C3_SDA |  |  |  |  |  |  | EVENTOUT
42 | PA8 | I/O | RCC_MCO |  | I2C3_SCL |  | I2C2_SDA | I2S2_MCK | TIM1_CH1 | USART1_CK | COMP7_OUT |  | TIM4_ETR | FDCAN3_RX | SAI1_CK2 | HRTIM1_CHA1 | SAI1_SCK_A | EVENTOUT
43 | PA9 | I/O |  |  | I2C3_SMBA |  | I2C2_SCL | I2S3_MCK | TIM1_CH2 | USART1_TX | COMP5_OUT | TIM15_BKIN | TIM2_CH3 |  |  | HRTIM1_CHA2 | SAI1_FS_A | EVENTOUT
44 | PA10 | I/O |  | TIM17_BKIN |  | CRS_SYNC | I2C2_SMBA | SPI2_MISO | TIM1_CH3 | USART1_RX | COMP6_OUT |  | TIM2_CH4 | TIM8_BKIN | SAI1_D1 | HRTIM1_CHB1 | SAI1_SD_A | EVENTOUT
45 | PA11 | I/O |  |  |  |  |  | I2S2_SD/SPI2_MOSI | TIM1_CH1N | USART1_CTS/USART1_NSS | COMP1_OUT | FDCAN1_RX | TIM4_CH1 | TIM1_CH4 | TIM1_BKIN2 | HRTIM1_CHB2 |  | EVENTOUT
46 | PA12 | I/O |  | TIM16_CH1 |  |  |  | I2S_CKIN | TIM1_CH2N | USART1_DE/USART1_RTS | COMP2_OUT | FDCAN1_TX | TIM4_CH2 | TIM1_ETR |  | HRTIM1_FLT1 |  | EVENTOUT
47 | VSS | Power
48 | VDD | Power
49 | PA13 | I/O | SYS_JTMS-SWDIO | TIM16_CH1N |  | I2C4_SCL | I2C1_SCL | IR_OUT |  | USART3_CTS/USART3_NSS |  |  | TIM4_CH3 |  |  | SAI1_SD_B |  | EVENTOUT
50 | PA14 | I/O | SYS_JTCK-SWCLK | LPTIM1_OUT |  | I2C4_SMBA | I2C1_SDA | TIM8_CH2 | TIM1_BKIN | USART2_TX |  |  |  |  |  | SAI1_FS_B |  | EVENTOUT
51 | PA15 | I/O | SYS_JTDI | TIM2_CH1 | TIM8_CH1 |  | I2C1_SCL | SPI1_NSS | I2S3_WS/SPI3_NSS | USART2_RX | UART4_DE/UART4_RTS | TIM1_BKIN |  | FDCAN3_TX |  | HRTIM1_FLT2 | TIM2_ETR | EVENTOUT
52 | PC10 | I/O |  |  |  |  | TIM8_CH1N | UART4_TX | I2S3_CK/SPI3_SCK | USART3_TX |  |  |  |  |  | HRTIM1_FLT6 |  | EVENTOUT
53 | PC11 | I/O |  |  |  | HRTIM1_EEV2 | TIM8_CH2N | UART4_RX | SPI3_MISO | USART3_RX | I2C3_SDA |  |  |  |  |  |  | EVENTOUT
54 | PC12 | I/O |  | TIM5_CH2 |  | HRTIM1_EEV1 | TIM8_CH3N | UART5_TX | I2S3_SD/SPI3_MOSI | USART3_CK |  |  |  |  |  |  | UCPD1_FRSTX1/UCPD1_FRSTX2 | EVENTOUT
55 | PD2 | I/O |  |  | TIM3_ETR |  | TIM8_BKIN | UART5_RX |  |  |  |  |  |  |  |  |  | EVENTOUT
56 | PB3 | I/O | SYS_JTDO-SWO | TIM2_CH2 | TIM4_ETR | CRS_SYNC | TIM8_CH1N | SPI1_SCK | I2S3_CK/SPI3_SCK | USART2_TX |  |  | TIM3_ETR | FDCAN3_RX | HRTIM1_SCOUT | HRTIM1_EEV9 | SAI1_SCK_B | EVENTOUT
57 | PB4 | I/O | SYS_JTRST | TIM16_CH1 | TIM3_CH1 |  | TIM8_CH2N | SPI1_MISO | SPI3_MISO | USART2_RX | UART5_DE/UART5_RTS |  | TIM17_BKIN | FDCAN3_TX |  | HRTIM1_EEV7 | SAI1_MCLK_B | EVENTOUT
58 | PB5 | I/O |  | TIM16_BKIN | TIM3_CH2 | TIM8_CH3N | I2C1_SMBA | SPI1_MOSI | I2S3_SD/SPI3_MOSI | USART2_CK | I2C3_SDA | FDCAN2_RX | TIM17_CH1 | LPTIM1_IN1 | SAI1_SD_B | HRTIM1_EEV6 | UART5_CTS | EVENTOUT
59 | PB6 | I/O |  | TIM16_CH1N | TIM4_CH1 |  |  | TIM8_CH1 | TIM8_ETR | USART1_TX | COMP4_OUT | FDCAN2_TX | TIM8_BKIN2 | LPTIM1_ETR | HRTIM1_SCIN | HRTIM1_EEV4 | SAI1_FS_B | EVENTOUT
60 | PB7 | I/O |  | TIM17_CH1N | TIM4_CH2 | I2C4_SDA | I2C1_SDA | TIM8_BKIN |  | USART1_RX | COMP3_OUT |  | TIM3_CH4 | LPTIM1_IN2 |  | HRTIM1_EEV3 | UART4_CTS | EVENTOUT
61 | PB8-BOOT0 | I/O |  | TIM16_CH1 | TIM4_CH3 | SAI1_CK1 | I2C1_SCL |  |  | USART3_RX | COMP1_OUT | FDCAN1_RX | TIM8_CH2 |  | TIM1_BKIN | HRTIM1_EEV8 | SAI1_MCLK_A | EVENTOUT
62 | PB9 | I/O |  | TIM17_CH1 | TIM4_CH4 | SAI1_D2 | I2C1_SDA |  | IR_OUT | USART3_TX | COMP2_OUT | FDCAN1_TX | TIM8_CH3 |  | TIM1_CH3N | HRTIM1_EEV5 | SAI1_FS_A | EVENTOUT
63 | VSS | Power
64 | VDD | Power

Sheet: NXP15XH103F03RC
NTC P/N (assuming ODESC 4p2 uses same BOM as ODRIVE 3.5) | NXP15XH103F03RC
V_TEMP = AVCC / (R_NTC + R_BOT) * R_BOT
CNTS = V_TEMP / AVCC * RESOLUTION
BITS | 12
RESOLUTION | 4096
AVCC | 3.3
R_BOT | 3300
 |  |  |  |  | 274.15
 |  | B (25-100C) | 10000 | R_t2 | t1 | t2 | Counts
 |  | 3455 | 10000 | 246828.5008 | 25 | -40 | 54.03942356
 |  | 3455 | 10000 | 134872.7513 | 25 | -30 | 97.82536622
 |  | 3455 | 10000 | 77287.26618 | 25 | -20 | 167.7287324
 |  | 3455 | 10000 | 46195.60784 | 25 | -10 | 273.0908982
 |  | 3455 | 10000 | 28668.09919 | 25 | 0 | 422.821511 | B(1/t+1/t) = ln(Rt1/Rt2)
 |  | 3455 | 10000 | 18398.44349 | 25 | 10 | 622.9386917
 |  | 3455 | 10000 | 12169.13864 | 25 | 20 | 873.7913802 | e^(B(1/t+1/t)) = Rt1/Rt2
 |  | 3455 | 10000 | 8270.721136 | 25 | 30 | 1168.189937
 |  | 3455 | 10000 | 5761.086466 | 25 | 40 | 1491.741642
 |  | 3455 | 10000 | 4103.502361 | 25 | 50 | 1825.730491
 |  | 3455 | 10000 | 2982.801527 | 25 | 60 | 2151.396943
 |  | 3455 | 10000 | 2208.740042 | 25 | 70 | 2453.700828
 |  | 3455 | 10000 | 1663.54084 | 25 | 80 | 2723.217243
 |  | 3455 | 10000 | 1272.576479 | 25 | 90 | 2956.05772
 |  | 3455 | 10000 | 987.5377919 | 25 | 100 | 3152.578626
 |  | 3455 | 10000 | 776.5282567 | 25 | 110 | 3315.762617
 |  | 3455 | 10000 | 618.0990823 | 25 | 120 | 3449.836187
 |  | 3455 | 10000 | 497.5801107 | 25 | 130 | 3559.319252
 |  | 3455 | 10000 | 404.777874 | 25 | 140 | 3648.477847
 |  | 3455 | 10000 | 332.5045702 | 25 | 150 | 3721.068959
 |  | 3455 | 10000 | 275.6217456 | 25 | 160 | 3780.265633
 |  | 3455 | 10000 | 230.4085315 | 25 | 170 | 3828.678715
 |  | 3455 | 10000 | 194.1379642 | 25 | 180 | 3868.421951
 |  | 3455 | 10000 | 164.7888159 | 25 | 190 | 3901.19015
 |  | 3455 | 10000 | 140.8469788 | 25 | 200 | 3928.335111
 |  |  | -40
 |  |  | -30
 |  |  | -20
 |  |  | -10
 |  |  | 0
 |  |  | 10
 |  |  | 20
 |  |  | 30
 |  |  | 40
 |  |  | 50
 |  |  | 60
 |  |  | 70
 |  |  | 80
 |  |  | 90
 |  |  | 100
 |  |  | 110
 |  |  | 120
 |  |  | 130
 |  |  | 140
 |  |  | 150
 |  |  | 160
 |  |  | 170
 |  |  | 180
 |  |  | 190
 |  |  | 200

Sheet: PLL config
 |  |  |  | P | 7, 17, 2-31
out | in | n | m | R, Q | 2, 4, 6, 8
340 | 16 | 85 | 4 | M | 1 to 16
 |  |  |  | N | 8 to 127
21.25 | 170

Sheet: LED Q shaped Pulse LUT
scaled from 0 to 1 as a float, then multiplied by 100 and converted to a uint
 | 0 | 1.00000000 | f | , | 255
 | 1 | 0.91514166 | f | , | 233.3611231
 | 2 | 0.83961928 | f | , | 214.1029172
 | 3 | 0.77218348 | f | , | 196.9067874
 | 4 | 0.71178025 | f | , | 181.5039632
 | 5 | 0.65751623 | f | , | 167.6666393
 | 6 | 0.60863087 | f | , | 155.2008725
 | 7 | 0.56447393 | f | , | 143.9408522
 | 8 | 0.52448726 | f | , | 133.7442516
 | 9 | 0.48818995 | f | , | 124.488438
 | 10 | 0.45516614 | f | , | 116.0673646
 | 11 | 0.42505495 | f | , | 108.389012
 | 12 | 0.39754223 | f | , | 101.3732699
 | 13 | 0.37235364 | f | , | 94.95017722
 | 14 | 0.34924884 | f | , | 89.05845308
 | 15 | 0.32801673 | f | , | 83.64426586
 | 16 | 0.30847136 | f | , | 78.66019782
 | 17 | 0.29044851 | f | , | 74.06437094
 | 18 | 0.27380277 | f | , | 69.81970635
 | 19 | 0.25840508 | f | , | 65.89329472
 | 20 | 0.24414062 | f | , | 62.25585937
 | 21 | 0.23090705 | f | , | 58.88129692
 | 22 | 0.21861288 | f | , | 55.74628314
 | 23 | 0.20717621 | f | , | 52.82993381
 | 24 | 0.19652358 | f | , | 50.11351202
 | 25 | 0.18658892 | f | , | 47.58017493
 | 26 | 0.17731276 | f | , | 45.21475412
 | 27 | 0.16864143 | f | , | 43.00356457
 | 28 | 0.16052642 | f | , | 40.9342381
 | 29 | 0.15292383 | f | , | 38.9955779
 | 30 | 0.14579385 | f | , | 37.17743111
 | 31 | 0.13910030 | f | , | 35.47057702
 | 32 | 0.13281031 | f | , | 33.8666287
 | 33 | 0.12689391 | f | , | 32.35794639
 | 34 | 0.12132377 | f | , | 30.93756097
 | 35 | 0.11607493 | f | , | 29.59910622
 | 36 | 0.11112454 | f | , | 28.33675893
 | 37 | 0.10645171 | f | , | 27.14518555
 | 38 | 0.10203723 | f | , | 26.01949483
 | 39 | 0.09786351 | f | , | 24.95519564
 | 40 | 0.09391435 | f | , | 23.94815928
 | 41 | 0.09017485 | f | , | 22.99458581
 | 42 | 0.08663127 | f | , | 22.09097392
 | 43 | 0.08327096 | f | , | 21.23409389
 | 44 | 0.08008221 | f | , | 20.42096334
 | 45 | 0.07705422 | f | , | 19.6488254
 | 46 | 0.07417698 | f | , | 18.91512908
 | 47 | 0.07144122 | f | , | 18.21751152
 | 48 | 0.06883836 | f | , | 17.55378203
 | 49 | 0.06636042 | f | , | 16.92190765
 | 50 | 0.06400000 | f | , | 16.32
 | 51 | 0.06175021 | f | , | 15.74630346
 | 52 | 0.05960464 | f | , | 15.19918442
 | 53 | 0.05755734 | f | , | 14.67712146
 | 54 | 0.05560273 | f | , | 14.1786965
 | 55 | 0.05373563 | f | , | 13.7025867
 | 56 | 0.05195120 | f | , | 13.24755705
 | 57 | 0.05024492 | f | , | 12.81245366
 | 58 | 0.04861254 | f | , | 12.39619764
 | 59 | 0.04705012 | f | , | 11.99777942
 | 60 | 0.04555394 | f | , | 11.61625364
 | 61 | 0.04412053 | f | , | 11.25073444
 | 62 | 0.04274663 | f | , | 10.90039111
 | 63 | 0.04142919 | f | , | 10.56444417
 | 64 | 0.04016534 | f | , | 10.24216165
 | 65 | 0.03895238 | f | , | 9.932855842
 | 66 | 0.03778777 | f | , | 9.635880118
 | 67 | 0.03666912 | f | , | 9.350626149
 | 68 | 0.03559420 | f | , | 9.076521268
 | 69 | 0.03456089 | f | , | 8.813026053
 | 70 | 0.03356718 | f | , | 8.559632104
 | 71 | 0.03261122 | f | , | 8.315859972
 | 72 | 0.03169120 | f | , | 8.081257264
 | 73 | 0.03080548 | f | , | 7.855396869
 | 74 | 0.02995245 | f | , | 7.637875331
 | 75 | 0.02913063 | f | , | 7.428311334
 | 76 | 0.02833861 | f | , | 7.226344293
 | 77 | 0.02757503 | f | , | 7.031633056
 | 78 | 0.02683865 | f | , | 6.843854691
 | 79 | 0.02612825 | f | , | 6.66270336
 | 80 | 0.02544270 | f | , | 6.487889273
 | 81 | 0.02478093 | f | , | 6.319137717
 | 82 | 0.02414191 | f | , | 6.156188142
 | 83 | 0.02352468 | f | , | 5.998793325
 | 84 | 0.02292831 | f | , | 5.846718574
 | 85 | 0.02235193 | f | , | 5.699740997
 | 86 | 0.02179470 | f | , | 5.557648816
 | 87 | 0.02125585 | f | , | 5.420240722
 | 88 | 0.02073461 | f | , | 5.287325282
 | 89 | 0.02023028 | f | , | 5.158720373
 | 90 | 0.01974217 | f | , | 5.03425266
 | 91 | 0.01926964 | f | , | 4.913757107
 | 92 | 0.01881206 | f | , | 4.797076515
 | 93 | 0.01836887 | f | , | 4.68406109
 | 94 | 0.01793948 | f | , | 4.574568042
 | 95 | 0.01752338 | f | , | 4.468461207
 | 96 | 0.01712004 | f | , | 4.365610684
 | 97 | 0.01672899 | f | , | 4.265892511
 | 98 | 0.01634976 | f | , | 4.169188344
 | 99 | 0.01598190 | f | , | 4.075385164
 | 100 | 0.01562500 | f | , | 3.984375
 | 101 | 0.01527865 | f | , | 3.896054667
 | 102 | 0.01494245 | f | , | 3.810325522
 | 103 | 0.01461605 | f | , | 3.72709323
 | 104 | 0.01429909 | f | , | 3.646267549
 | 105 | 0.01399122 | f | , | 3.567762121
 | 106 | 0.01369213 | f | , | 3.491494282
 | 107 | 0.01340151 | f | , | 3.417384875
 | 108 | 0.01311905 | f | , | 3.345358081
 | 109 | 0.01284448 | f | , | 3.275341254
 | 110 | 0.01257751 | f | , | 3.207264769
 | 111 | 0.01231789 | f | , | 3.141061874
 | 112 | 0.01206537 | f | , | 3.076668553
 | 113 | 0.01181970 | f | , | 3.0140234
 | 114 | 0.01158066 | f | , | 2.953067489
 | 115 | 0.01134802 | f | , | 2.893744264
 | 116 | 0.01112157 | f | , | 2.835999425
 | 117 | 0.01090110 | f | , | 2.779780825
 | 118 | 0.01068642 | f | , | 2.725038371
 | 119 | 0.01047735 | f | , | 2.671723929
 | 120 | 0.01027369 | f | , | 2.619791239
 | 121 | 0.01007528 | f | , | 2.569195824
 | 122 | 0.00988194 | f | , | 2.519894916
 | 123 | 0.00969352 | f | , | 2.471847379
 | 124 | 0.00950986 | f | , | 2.425013633
 | 125 | 0.00933081 | f | , | 2.379355591
 | 126 | 0.00915622 | f | , | 2.33483659
 | 127 | 0.00898597 | f | , | 2.291421329
 | 128 | 0.00881991 | f | , | 2.249075815
 | 129 | 0.00865791 | f | , | 2.207767301
 | 130 | 0.00849986 | f | , | 2.167464237
 | 131 | 0.00834563 | f | , | 2.128136217
 | 132 | 0.00819511 | f | , | 2.089753932
 | 133 | 0.00804819 | f | , | 2.052289124
 | 134 | 0.00790476 | f | , | 2.015714542
 | 135 | 0.00776472 | f | , | 1.980003902

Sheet: Pinout OLD
 |  | Odrive Pinout | Notes | Tested | Respective Peripheral
#define | GPIO1 | PA0 | encoder push button | yes
#define | GPIO2 | PA1 | soft button/timing | yes
#define | GPIO3 | PA2 | use as uart4 TX | yes | UART4
#define | GPIO4 | PA3 | Use as Uart4 Rx | yes | UART4
#define | SPI_MOSI | PC12 |  | yes
#define | SPI_MISO | PC11 |  | yes
#define | SPI_SCK | PC10 |  | yes
#define | SPI_CS_IO6 | PB2 |  | yes
#define | SPI_nCS_DRV | PC13 | internal to board | yes
#define | CAN_TX | PB9 |  | yes
#define | CAN_RX | PB8 |  | yes
#define | ENC_A | PB4 |  | yes
#define | ENC_B | PB5 |  | yes
#define | ENC_Z | PC9 |  | yes
#define | USB_DM D- | PA11 | repurposed as encoder rotary pos
#define | USB_DP__LED_DO | PA12 | used for sending info to WS2812B LED's
#define | AUX_H | PB11 | repurposed as ssd1357 CS | Yes
#define | AUX_L | PB10 | repurposed as ssd1357 D# | Yes
 | Boot |  | dedicated boot0 pin :(
#define | DC_CAL |  | These are not connected to the MCU in the Odrive 3.5 schematic
#define | nOCTW
#define | nFAULT | PD2
#define | EN_GATE | PB12 |  | yes
#define | AH | PA8 |  | yes |  | TIM1
#define | AL | PB13 |  | yes |  | TIM1
#define | BH | PA9 |  | yes |  | TIM1
#define | BL | PB14 |  | yes |  | TIM1
#define | CH | PA10 |  | yes |  | TIM1
#define | CL | PB15 |  | yes |  | TIM1
#define | SO1 | PC0
#define | SO2 | PC1
#define | M_TEMP | PC5 | P/N: NXP15XH103F03RC
#define | AUX_TEMP | PA5 | P/N: NXP15XH103F03RC , repurpose as SSD1357 nRST
#define | VBUS_SNS | PA6 | Top: 10k, Bottom, 1K

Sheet: LED Driver
logic 0 high | 0.35
logic 0 low | 0.8
 | 1.15
logic 1 high | 0.7
logic 1 low | 0.6
 | 1.3
1.2
0.25
0.125 |  | periodicity | 3e-07 | 300ns |  | SYSCLK freq | 168000000
0.475 |  | freq | 3333333.333 | 3.34MHz |  | clk divider | 50
 |  |  |  |  | 50.40 | actual dma bump freq | 3360000
 |  | bits per led | 24 |  |  | dma bump periodicity | 2.976190476e-07
 |  | comm time per led | 7.2e-06
 |  | # of LED's | 50
 |  | reset time | 7.5e-05
 |  | time per transmission | 0.000435 | 435uS
 |  | num of total data bits | 1200
 |  | num of transfers data | 4800
 |  | num of transfers reset | 250
 |  | num of dma transfers | 5050
 |  | number of bytes per transfer | 2
 |  | num of bytes required | 10100

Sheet: Shunt Value Calculation
 | 150ma q current measured
 | 10mOhm shunt
zero | 2015
max 1 sensor curr | 1880
counts | 135
volts | 3.3
bits resolution | 4096
voltage at ADC pin | 0.1087646484
gain | 80
shunt resistance | 0.01
V = I*R*Gain
I = V/(R*Gain) | 0.1359558105
intended max amperage reading | 0.4
intended gain | 40
max unidirectional voltage (w/ margin) | 1.5
V = I*R*Gain
R = V/(I*Gain) | 0.09375
R = 100mOhm
Power = V*I | 0.015

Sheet: CAN Notes
11 | curr setpoint
11 | q curr
11 | phi dot
11 | theta dot
8 | phi
8 | theta
2 | state
2 | rolling counter
64

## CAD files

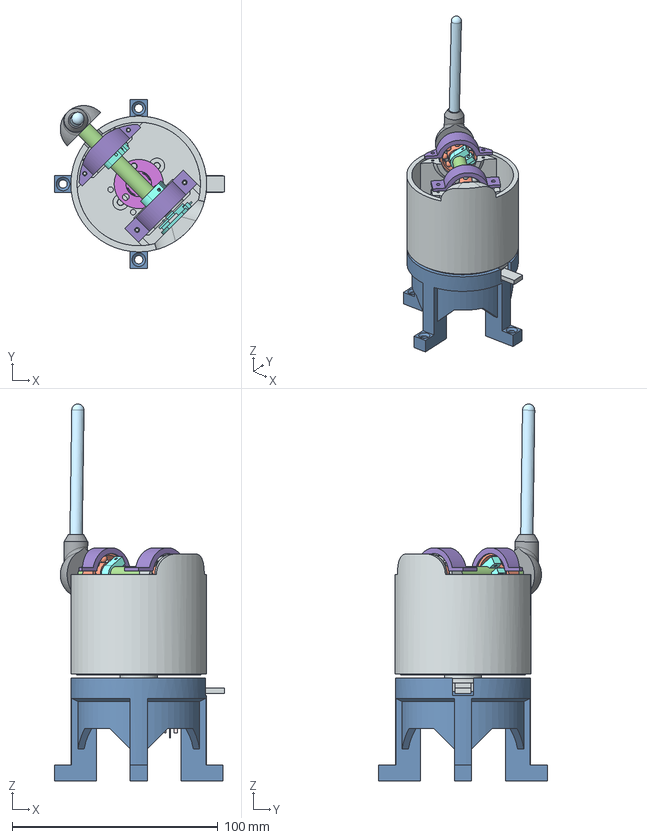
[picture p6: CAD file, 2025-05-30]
mechanical/Assembly.step
82.7 x 82.0 x 183.1 mm
Pendulum Moment
608 Bearings x 4
Friction Circlip x 2
Encoder AMT103
Pendulum Axle
Motor GB54-2
Pendulum Axle to Moment Adapter 6mm shaft v4
Front Bearing Clamp
Upper Rotor Base
8mm_ID_Alum_Tube
Mag Sensor
Encoder Shaft Adapter Sleeve
slip_ring
Encoder Shaft Coupler A
Rear Bearing Clamp
Encoder To Motor Mount
Encoder Shaft Coupler B

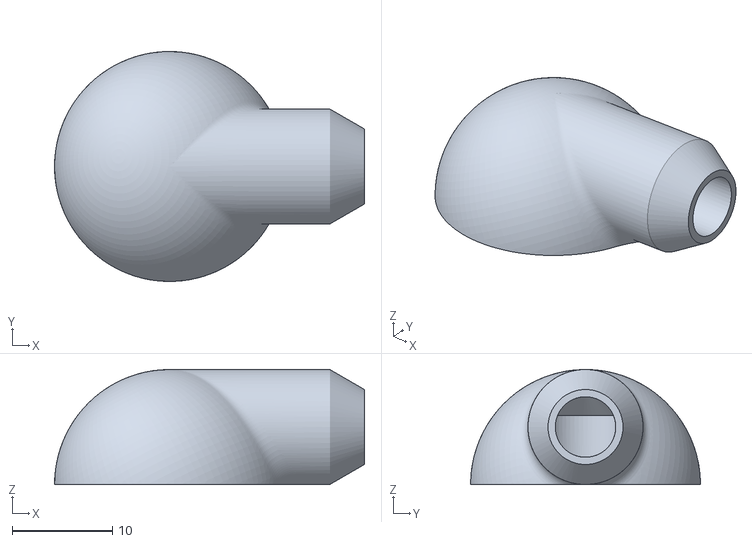
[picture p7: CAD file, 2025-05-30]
mechanical/V1_Files_STL/Pendulum Axle to Moment Adapter 6mm shaft version.stl
31.0 x 23.0 x 11.5

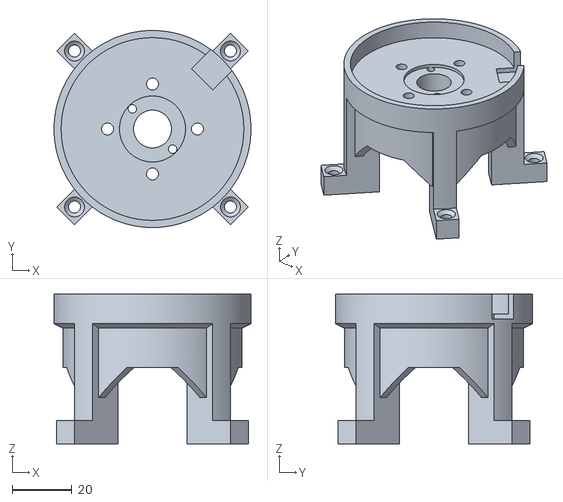
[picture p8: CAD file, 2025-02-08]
mechanical/V1_Files_STL/Motor Test Mount.stl
65.7 x 65.7 x 50.0

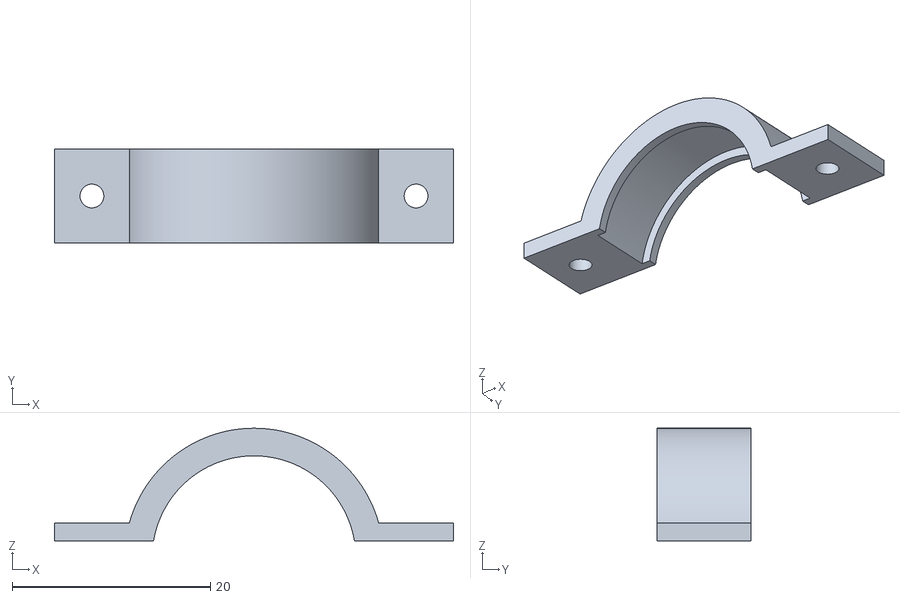
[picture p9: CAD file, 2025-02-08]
mechanical/V1_Files_STL/Rear Bearing Clamp.stl
40.2 x 9.50 x 11.3

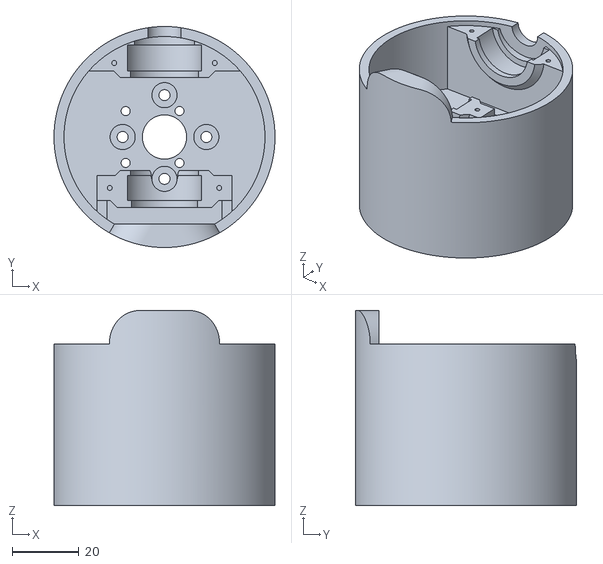
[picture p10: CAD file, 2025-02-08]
mechanical/V1_Files_STL/Upper Rotor Base.stl
66.0 x 66.0 x 58.3

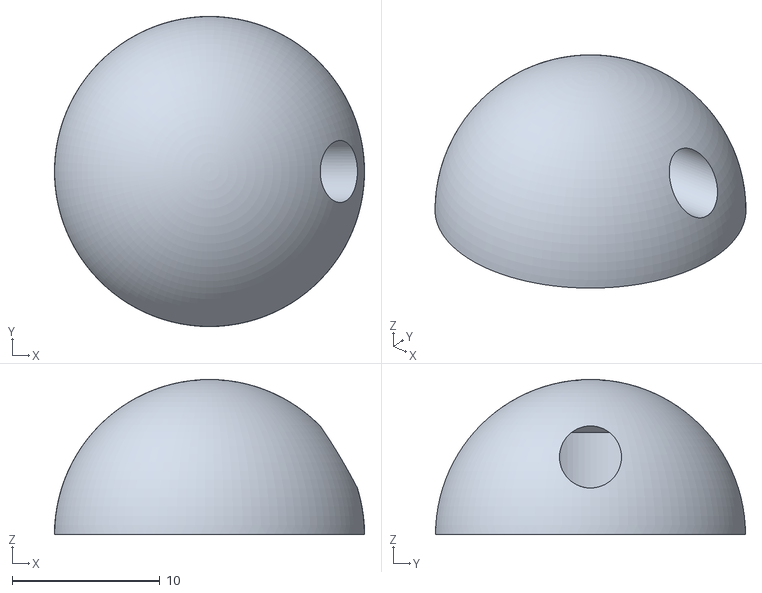
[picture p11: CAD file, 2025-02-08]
mechanical/V1_Files_STL/Pendulum Axle to Moment Adapter V2.stl
21.0 x 21.0 x 10.5

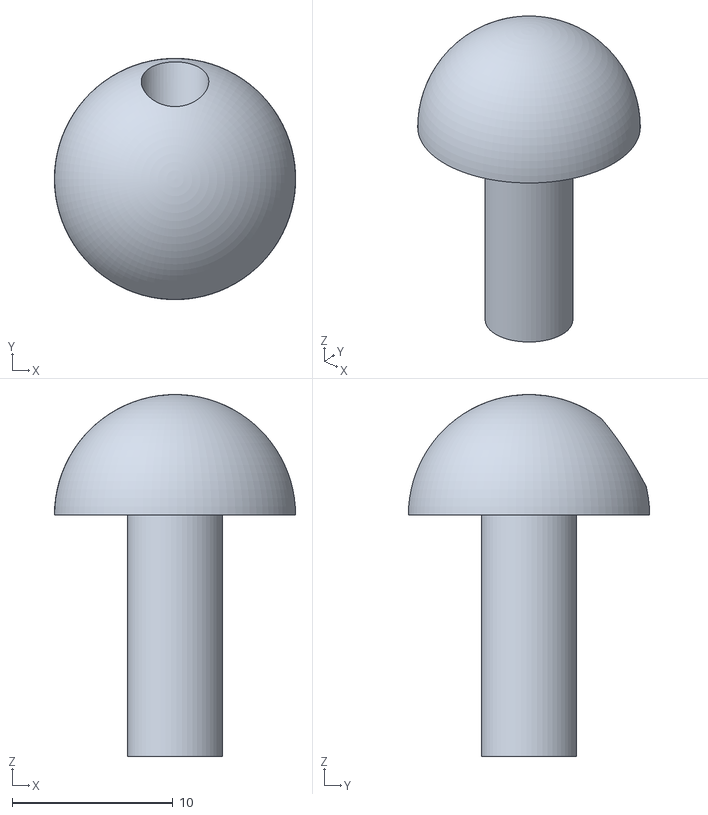
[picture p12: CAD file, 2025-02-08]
mechanical/V1_Files_STL/Pedulum Axle To Moment Adapter.stl
15.0 x 15.0 x 22.5

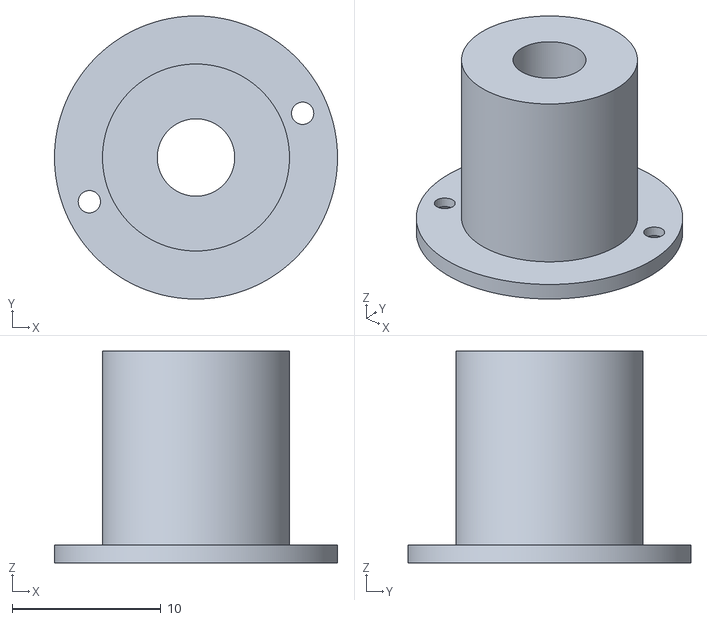
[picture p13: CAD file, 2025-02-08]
mechanical/V1_Files_STL/Encoder Shaft Adapter Sleeve.stl
19.0 x 19.0 x 14.2

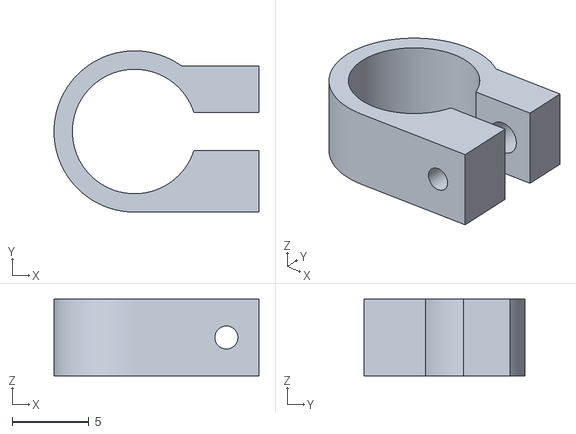
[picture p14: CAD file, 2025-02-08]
mechanical/V1_Files_STL/Friction Circlip.stl
13.3 x 10.5 x 5.00

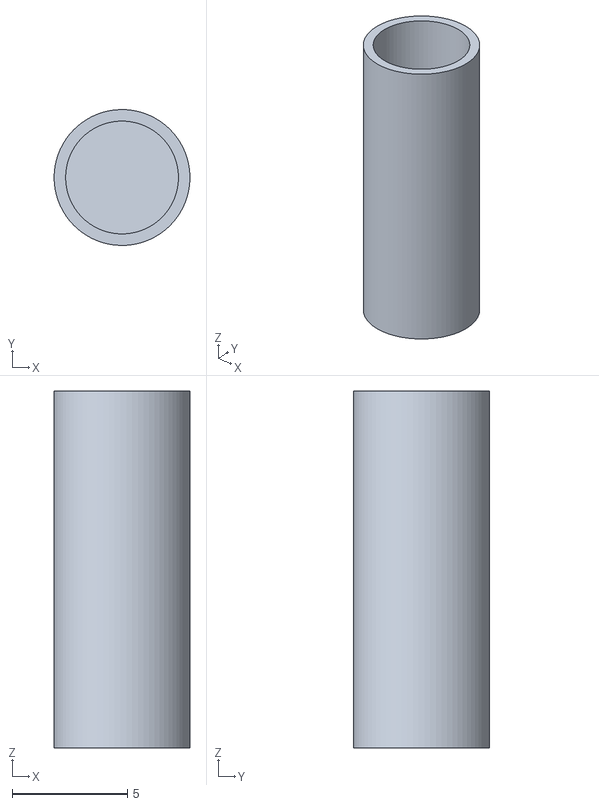
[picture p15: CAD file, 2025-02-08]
mechanical/V1_Files_STL/Magnet to Pendulum Axle Adapter v1.stl
5.90 x 5.90 x 15.5

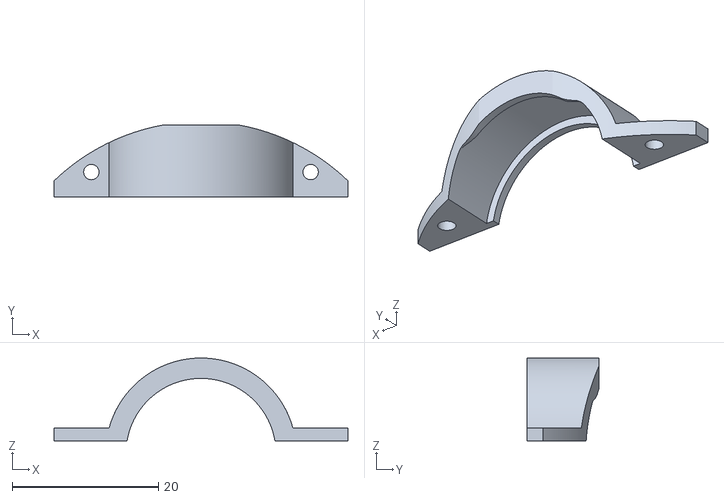
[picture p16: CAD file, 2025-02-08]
mechanical/V1_Files_STL/Front Bearing Clamp.stl
40.2 x 9.80 x 11.3

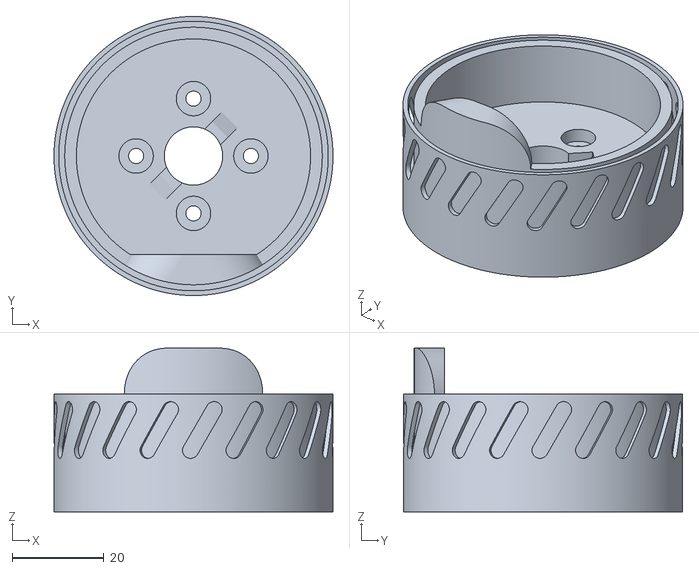
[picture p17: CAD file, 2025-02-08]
mechanical/V1_Files_STL/Upper Rotor Base 2p0.stl
60.8 x 60.8 x 35.7

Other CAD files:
mechanical/V1_STEP/Pendulum Axle to Moment Adapter 6mm shaft.step

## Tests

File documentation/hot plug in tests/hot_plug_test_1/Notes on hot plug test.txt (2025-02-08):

CC-65 current sensor used, on 10mV/A scaling (20kHz bandwidth....)

yellow is 20V measured at board, blue is current

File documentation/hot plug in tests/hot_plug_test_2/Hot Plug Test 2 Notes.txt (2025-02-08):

Tested with a more powerful 170W version of the lenovo chargers.  

This was measured with a much more expensive scope and current sensor than the first hot plug test.  

The yellow signal is the voltage measured at the input of the motor controller using the tektronix passive probe that came with the scope

the green signal is the inrush current after attaching the connector to the harness I made.  It was measured using a very high bandwidth, +/- 300A rogowski coil.

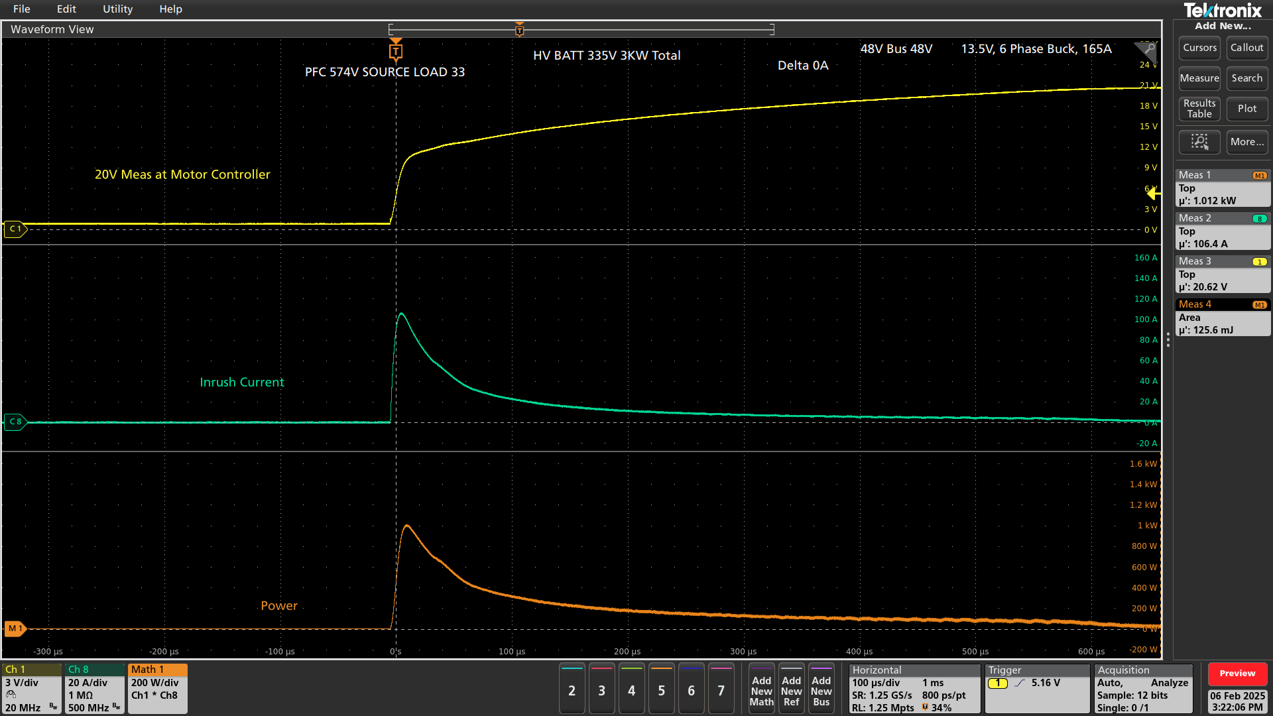
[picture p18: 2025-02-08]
documentation/hot plug in tests/hot_plug_test_2/ODESC V4p2 Hot plug.png

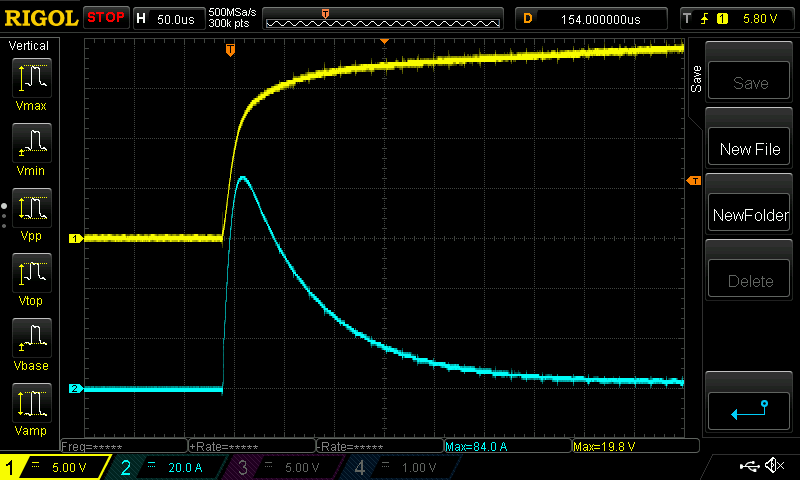
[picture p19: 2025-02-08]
documentation/hot plug in tests/hot_plug_test_1/Lenovo 20V charger (ADL135NLC3A) to ODESC4p2 hot plug.png

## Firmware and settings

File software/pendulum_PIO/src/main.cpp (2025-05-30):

#include <Arduino.h>
#include "STM32_CAN.h"
#include "../lib/Arduino-FOC/src/SimpleFOC.h"


#include "Drivers/DRV8301_Gate_Driver/DRV8301_Gate_Driver.hpp" 
#include "Drivers/AS5048A_MagSenseSPI/AS5048A_MagSenseSPI.hpp" // mag sensor
#include "Drivers/WS2812B_RGB_LED_Strip/WS2812B_RGB_LED_Strip.hpp" // RGB LED's
#include "Drivers/ADC_Interface/ADC_Interface.hpp" 
#include "Drivers/SSD1357_RGB_OLED/OLED_Graphics.h" 

#include "../lib/Arduino-FOC/src/common/foc_utils.h" // sin, cosine, pi, 2pi, etc

#include "CAN_TP/can_tp.hpp"

#include "Biquad.hpp"

#include "gpio.h"
#include "config.hpp"
#include "Gimbal/gimbal.hpp"
#include "RGB_Wrapper/RGB_Wrapper.hpp"

#include "Pendulum/pendulum.hpp"





////////////////////////// DEFINITIONS: ////////////////////////////

#if !defined(_STM32_DEF_)
#define _STM32_DEF_
#endif 

#if !defined(SIMPLEFOC_STM32_DEBUG)
#define SIMPLEFOC_STM32_DEBUG
#endif 





//////////////////////////// CLASS: DECLARATIONS: ////////////////////////////


HardwareTimer ctrl_loop_5kHz_timer = HardwareTimer(TIM4);
//HardwareTimer test_tmr = HardwareTimer(TIM8);

/************* DRV8301: DRIVER: *************/
/** NOTE: both sw_bldc_driver and hw_bldc_driver classes have control over 
 * the EN_GATE, but the only time hw_bldc_driver uses it is on initialization. 
 * 
 * after the hw_bldc_driver's init function is called only the "sw_bldc_driver" class
 * has control of the EN_GATE pin. */
DRV8301_Gate_Driver hw_bldc_driver = DRV8301_Gate_Driver(SPI_nCS_DRV, EN_GATE, nFAULT);
void on_nFAULT() { hw_bldc_driver.fault_pin_asserted_isr_callback(); }


/************* MAG: SENSE: *************/
AS5048A_MagSenseSPI mag_sense = AS5048A_MagSenseSPI(SPI_nCS_IO6);

/** Params are: MOSI, MISO, SCLK, Chip select (optional). Chip select will be controlled 
 * by the calling function. */
SPIClass SPI_2(SPI_MOSI, SPI_MISO, SPI_SCK); 


/************* COMM: *************/
HardwareSerial hw_serial(GPIO4_UART_RX, GPIO3_UART_TX);

Commander command = Commander(hw_serial);// commander interface
void on_motor(char* cmd){ command.motor(&motor, cmd); }


WS2812B_RGB_LED_Strip led_strip = WS2812B_RGB_LED_Strip(USB_DP__LED_DO);
RGB_Wrapper rgb_wrapper = RGB_Wrapper(40);

OLED_Graphics oled = OLED_Graphics();











////////////////////////////////// 5kHz: CONTROL: LOOP: ISR: /////////////////////////////////

void Update_IT_callback(void)
{
  //digitalWrite(GPIO2__SSD_nRST, HIGH); 
  
  pdm_run_control_loop();
  
  /** pack and send CAN msg */
  send_can_Debug1_message(motor.current_sp,
                          motor.current.q,
                          pdm.pdm_theta_dot_filt,
                          motor.shaft_velocity,
                          pdm.pdm_phi,
                          encoder.getMechanicalAngle(),
                          0);
  
  //digitalWrite(GPIO2__SSD_nRST, LOW); 
}







////////////////////////////////// SETUP: /////////////////////////////////

void setup() 
{
  hw_serial.begin(250000); 

  /** only used for timing analysis for now */
  //pinMode(GPIO1__SSD_nCS, OUTPUT);
  //pinMode(GPIO2__SSD_nRST, OUTPUT);
  //digitalWrite(GPIO1__SSD_nCS, LOW);
  //digitalWrite(GPIO2__SSD_nRST, LOW);
  
  rgb_wrapper.link_ws2812b_rgb_led_driver_class(&led_strip);
  rgb_wrapper.init_periphs_for_WS2812B();
  
  RGB_Wrapper_HV_Color_s tmp_led_init_color_blink;
  tmp_led_init_color_blink.hue = 150.0f;  // static hue
  tmp_led_init_color_blink.value = 128;  // static value
  
  RGB_Wrapper_HV_Color_s tmp_led_init_color_pulse;
  tmp_led_init_color_pulse.hue = 330.0f;  //static hue
  tmp_led_init_color_pulse.value = 255;  // max value
  
  RGB_Wrapper_HV_Color_s tmp_led_init_color_circle;
  tmp_led_init_color_circle.hue = 30.0f;
  tmp_led_init_color_circle.value = 128.0f; //30;
  
  
  /** initialize pixel and led circle configuration: */
  //rgb_wrapper.set_rainbow_pixel_settings(0, 1, 30, 120.0f, 0.1f);
  //rgb_wrapper.set_pulse_pixel_settings(2, 2, 80.0, 0.3f, false, tmp_led_init_color_pulse);
  //rgb_wrapper.set_blink_pixel_settings(3, 3, 0.0f, 0.025f, false, tmp_led_init_color_blink);
  rgb_wrapper.set_circle_pixel_settings(0, 39, \
                                        RGB_Wrapper_Circle__Phi_Rainbow_Theta_Q, \
                                        -0.307f, \
                                        0.001f, \
                                        6, \
                                        tmp_led_init_color_circle);
  //
  rgb_wrapper.set_theta_offset_in_radians(-1.264767f, RGB_Wrapper_Theta_Tracking_Direction__INVERSE);
  
  if(rgb_wrapper.finish_initializing_pixel_types() == RGB_Wrapper_Status_UPDATING_LED_BUF)
    hw_serial.println("LED types done initializing.");
  else  
    hw_serial.println("Failed to initialize LED's types/driver!");



  #if 1
  oled.begin(USB_DM__SSD_DS, GPIO2__SSD_nRST, GPIO1__SSD_nCS, SPI_2, 8000000);
  oled.fillDisplay(0); 
  oled.write('B');
  oled.write('O');
  oled.write('O');
  oled.write('T');
  oled.write('I');
  oled.write('N');
  oled.write('G');
  oled.write(' ');
  oled.write('U');
  oled.write('P');
  oled.write('.');
  oled.write('.');
  oled.write('.');
  
  #else 
  /** For RGB LED timing analysis: */
  pinMode(GPIO2__SSD_nRST, OUTPUT);
  digitalWrite(GPIO2__SSD_nRST, LOW);
  pinMode(GPIO1__SSD_nCS, OUTPUT);
  digitalWrite(GPIO1__SSD_nCS, LOW);
  pinMode(USB_DM__SSD_DS, OUTPUT);
  digitalWrite(USB_DM__SSD_DS, LOW);
  #endif 


  /** Prescaler is automatically set when setting overflow with format != tick */
  ctrl_loop_5kHz_timer.setOverflow(200UL, MICROSEC_FORMAT);
  ctrl_loop_5kHz_timer.attachInterrupt(Update_IT_callback);

  pinMode(AUX_H, OUTPUT); 
  pinMode(AUX_L, OUTPUT);
  digitalWrite(AUX_H, LOW);
  digitalWrite(AUX_L, LOW);

  /** Set as inputs to be configured in the simpleFOC's hardware specific
   * "_adc_init" in stm32f4_hal.cpp file, so we can measure bus voltage 
   * at 20kHz just like with current sensors so control loops can run on 
   * data. We don't use a brake resistor but future uses for the ODESC 
   * might. */
  pinMode(VBUS_SNS, INPUT);
  
  // init magnetic angle sensor
  if(mag_sense.init(&SPI_2) != true)
  {
    hw_serial.println("Failed to initialize AS5048A Mag Sensor!");

    /** return early, do not control the motor! */
    return;
  }
  
  mag_sense.update();
  
  pdm_set_theta_offset_when_pointed_down();
  
  if(hw_bldc_driver.init(DRV8301_GAIN_SETTING, &SPI_2, on_nFAULT) != true)
  {
    hw_serial.println("Failed to set gain settings for DRV8301!");

    /** return early, do not control the motor! */
    return;
  }

  can_tp_init();

  adc_if_init(&ctrl_loop_5kHz_timer);

  gimbal_init(hw_serial);

  oled.reconfigureSpiSettings(); 
  oled.write('D');
  oled.write('O');
  oled.write('N');
  oled.write('E');
  oled.write('\n');
  oled.write(' '); // '\n' character is ignored if the font's x position is 0.
  oled.write('\n'); 
  oled.write('M');
  oled.write('O');
  oled.write('T');
  oled.write('O');
  oled.write('R');
  oled.write(' ');
  oled.write('C');
  oled.write('O');
  oled.write('N');
  oled.write('F');
  oled.write('I');
  oled.write('G');
  oled.write('U');
  oled.write('R');
  oled.write('E');
  oled.write('D');

  pdm_torque_setpoint_biquad_c.set_steady_state_val(0.0f);

  command.add('M', on_motor,"my motor motion");
  command.add('C', pdm_on_constants,"Control Constants");

  command.run();
  motor.monitor();
  
  ctrl_loop_5kHz_timer.resume();

  motor.enable();
}








float hue = 0.0f;
uint8_t value = 30;

void loop() 
{
  #if 0
  led_strip.modify_pixel_buffer_all_leds(hue, value);

  hue += 0.01f;
  if(hue >= 360.0f)
  {
    hue = 0.0f;
  }

  if(led_strip.process_bitfield_array(55) == WS2812B_READY_TO_UPLOAD_BITSTREAM)
  {
    (void)led_strip.write_bitfield_array_via_dma();
  }
  #else
    //digitalWrite(USB_DM__SSD_DS, HIGH);
    rgb_wrapper.update_pixels(pdm.pdm_theta /** pdm.pdm_phi */, encoder.getMechanicalAngle());
    //digitalWrite(USB_DM__SSD_DS, LOW);
  #endif 

  
  //oled.write(value);
  if(value > 255)
  {
    value = 55;
    //oled.write(value);
  }
  else
    value++;

  command.run();
  motor.monitor();

  if(pdm.D == 1.0f)
  {
    hw_serial.print(pdm.pdm_phi, 6); //
    hw_serial.print("    ");
    hw_serial.print(pdm.pdm_theta_dot_filt, 6);
    hw_serial.print("    ");
    hw_serial.print(encoder.getVelocity(), 6);
    hw_serial.print("    ");
    hw_serial.print(encoder.getMechanicalAngle(), 6);
    hw_serial.print("    ");
    hw_serial.println(pdm.offset.median_phi_in_revolution, 6);
  }
  else if(pdm.D == 2.0f)
  {
    uint32_t test = adc_if_get_phB_LS_CS_SO1_counts();
    hw_serial.print(test); //
    hw_serial.print("    ");
    test = adc_if_get_phC_LS_CS_SO2_counts();
    hw_serial.print(test);
    hw_serial.print("    ");
    test = adc_if_get_vbus_counts();
    hw_serial.println(test);
  }
  else if(pdm.D == 3.0f)
  {
    float test = adc_if_get_vbus_v();
    hw_serial.print(test); //
    hw_serial.print("    ");
    test = adc_if_get_pcb_temp_near_motor_fets_C();
    hw_serial.print(test);
    hw_serial.print("    ");
    test = adc_if_get_pcb_temp_near_aux_fets_C();
    hw_serial.println(test);
  }

  pdm_run_phi_offset_correction_checks();
}

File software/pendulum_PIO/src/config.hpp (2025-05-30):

#ifndef __CONFIG_HPP
#define __CONFIG_HPP

/********************** TESTING: STUFF: ***********************/
/** In an implementation mistake, I gave the Bx coefficients
 * the wrong polarity, which on most slower cutoff biquad gains
 * caused some kind of FPU over/underflow that crashed a lot of things.
 * 
 * I haven't confirmed it's an FPU overflow but that seems like the 
 * most likely explanation.
 * 
 * NOTE: Causing the FPU to over/underflow like this seems to 
 * cause a lot of issues including over current faults on the 
 * DRV8301.  For this reason, we will use it to test 
 * fault detection and response on the DRV8301 driver. */
//#define CRASH_FPU_USING_WRONG_BIQUAD_GAIN_POLARITIES



/********************** GIMBAL: CONFIG: ***********************/

/** Dead zone as a percentage/factor of the switching period. 
 * The default value is 2% (or 0.02) but we are dividing that by 4
 * since it seems like way more than we need when looking at the 
 * H-bridge switch node voltage waveforms. 
 * 
 * With this new value the diodes on the H-bridges are conducting current
 * (hard switching, or partial/full ZVS) for about 140ns which seems 
 * appropriate. The MOSFET's that are used on the ODESC 4.2 have a part 
 * number of .
 * 
 * I couldn't find app notes for this family of FET's (P/N NTMFS5C628NL)
 * or recommended deadtime but the switching fall time (70ns) 
 * and the turn-off delay time (28ns)
 * are both well under the present deadtime. */
#define SW_BLDC_DRV__DEAD_ZONE__AS_FACTOR_OF_SW_PRD 0.005f

/** PSU voltage is what the sw driver uses to scale
 * the DQ voltage setpoints to the duty cycle 
 * of the h-bridges. */
#define SW_BLDC_DRV__V_PSU 20.0f
#define SW_BLDC_DRV__V_LIMIT 20.0f // this is only used for centering pwm phase voltages

/** set "pre foc init" limits to a low value in case there are issues 
 * with the HW before/during FOC init. 
 * NOTE: If MOTOR__V_LIMIT_PRE_FOC_INIT is < 3V, it will limit motor.voltage_sensor_align
 * voltage value from the default of 3.0 volts.  However,
 * with this motor we don't need to bother going below 3 volts during 
 * sensor alignment to the d axis.  */
#define MOTOR__V_LIMIT_PRE_FOC_INIT 4.0f 
#define MOTOR__V_LIMIT_POST_FOC_INIT 8.0f
#define MOTOR__I_LIMIT_PRE_FOC_INIT 1.0f
#define MOTOR__I_LIMIT_POST_FOC_INIT 1.0f

/** NOTE: low pass filter implementation can be found by ctrl+shift+f this:
 * LowPassFilter::operator() 
 * 
 * The LPF is an exponential filter with an alpha value of .tf/(.tf + dt) 
 * so it is a function of time delta between sensor readings */
#define MOTOR__VELOCITY_LPF_TF 0.04f  // old is 0.01f

#define MOTOR__Q_CURR_MEAS_FILT_TF  0.001f     // old is 0.004f
#define MOTOR__Q_CURR_PID_P_GAIN    200.0f     // old is 12
#define MOTOR__Q_CURR_PID_I_GAIN    100.0f     // old is 3
#define MOTOR__Q_CURR_PID_D_GAIN    0.0f
#define MOTOR__Q_CURR_PID_SAT_LIMIT     MOTOR__V_LIMIT_POST_FOC_INIT  // this is in units of voltage

#define MOTOR__D_CURR_MEAS_FILT_TF  0.02f       // old is 0.02f
#define MOTOR__D_CURR_PID_P_GAIN    0.0f     // old is 2000.0f
#define MOTOR__D_CURR_PID_I_GAIN    0.0f      // old is 600.0f
#define MOTOR__D_CURR_PID_D_GAIN    0.0f
#define MOTOR__D_CURR_PID_SAT_LIMIT     MOTOR__V_LIMIT_POST_FOC_INIT   // this is in units of voltage

/** To speed up startup time by over a second, we can
 * skip the pole pair, minimum movement, and direction checks 
 * by setting the "motor.sensor_direction" before calling initFOC.  
 * 
 * This requires:
 *   - Knowing what the direction is (on startup the detected 
 *     direction is printed out via serial comm)
 *   - Knowing there is not an issue with the physical 
 *     construction, wiring, or circuitry of the pendulum.  */
#define SKIP_POLE_PAIR_AND_DIRECTION_CHECKS

#ifdef SKIP_POLE_PAIR_AND_DIRECTION_CHECKS
#define MOTOR__SENSOR_DIRECTION    Direction::CW
#else
#define MOTOR__SENSOR_DIRECTION    Direction::UNKNOWN
#endif 





/** Number of pole pairs on the the GB54-1 is 7, config is 12n14p */
#define NUM_OF_POLE_PAIRS 7

/** Encoder Pulse/Counts per Revolution = 2048 AM103, default switch config */
#define ENCODER_PPR 2048UL

/** Shunt Resistor Resistance in Ohms 
 * NOTE: 500uOhms is default for the ODESC 4.2, but i've replaced the value
 * with a 10mOhm shunt to get better resolution for the amperage the phases 
 * will see in the GB54-2 gimbal motor. */
#define SHUNT_RESISTANCE_OHMS 0.200f 

/** Even with 80V/V of gain, 10mOhm may be too small of a value.
 * Next batch of electronics parts I buy I'll get a 100mOhm sensor to 
 * try out. */

/** Lowside Motor Current sensor gain. 
 * This can be changed via spi comms by writing to a reg, by default it's 10. */
#define MOTOR_CURR_SNS_GAIN 10.0f 
#define DRV8301_GAIN_SETTING DRV8301_GainSetting_10_V_over_V






#endif // __CONFIG_H

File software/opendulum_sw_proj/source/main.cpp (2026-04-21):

#include <stdint.h>
// #include <math.h>

#include "stm32g4xx_hal.h"
#include "stm32g4xx.h"
#include "system_stm32g4xx.h"

// #include "stm32g4xx_hal_flash.h"
// #include "stm32g4xx_ll_bus.h"


// #include "stm32g4xx_ll_rcc.h"
// #include "stm32g4xx_ll_crs.h"
// #include "stm32g4xx_ll_system.h"
// #include "stm32g4xx_ll_exti.h"
// #include "stm32g4xx_ll_cortex.h"
// #include "stm32g4xx_ll_utils.h"
// #include "stm32g4xx_ll_pwr.h"
// #include "stm32g4xx_ll_dma.h"
// #include "stm32g4xx_ll_gpio.h"
// #include "stm32g4xx_hal_rcc.h"

#include "pins.hpp"
#include "WS2812B_RGB_LED_Strip.hpp"
#include "OS_Tick.hpp"

extern "C" {
  #include "startup.h"
}


#if !defined(__SOFT_FP__) && defined(__ARM_FP)
  #warning "FPU is not initialized, but the project is compiling for an FPU. Please initialize the FPU before use."
#endif


WS2812B_RGB_LED_Strip rbg_led_strip_drv = WS2812B_RGB_LED_Strip(&gpio_led_data_out);

OS_Tick os_tick = OS_Tick(TIM2);

HAL_StatusTypeDef startup_status; // tracks startup status, unused for now

float test = 0.0f;




int main(void)
{
  startup_status = startup_run();

  (void)os_tick.configure_os_tick_timer();
  
  pins_configure_gpio();

  rbg_led_strip_drv.set_gpio_pin_level(1);
  rbg_led_strip_drv.set_gpio_pin_level(0);

  rbg_led_strip_drv.init_dma_and_timer_peripherals(20);

  rbg_led_strip_drv.modify_pixel_buffer_all_leds(66.0f, 20);
  rbg_led_strip_drv.process_bitfield_array(20);
  rbg_led_strip_drv.write_bitfield_array_via_dma();


  while (1)
  {
    test += 5.023401f;
    gpio_led1.set_pin_level_high();
    gpio_led2.set_pin_level_high();
    os_tick.wait_us(1000000);
    gpio_led1.set_pin_level_low();
    gpio_led2.set_pin_level_low();
    os_tick.wait_us(1000000);
  }
}

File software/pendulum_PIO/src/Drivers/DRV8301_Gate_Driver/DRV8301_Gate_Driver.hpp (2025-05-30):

#ifndef __DRV8301_HPP
#define __DRV8301_HPP

#include "Arduino.h"
#include <SPI.h>

/** NOTE: This file has been adapted from the DRV8301 driver found 
 * in the most recent version of the ODrive 3.5 open source software. 
 */

/** Datasheet Section 7.6.3.2 */
typedef enum : uint16_t {
    DRV8301_GainSetting_10_V_over_V  = 0, 
    DRV8301_GainSetting_20_V_over_V  = 1, 
    DRV8301_GainSetting_40_V_over_V  = 2, 
    DRV8301_GainSetting_80_V_over_V  = 3, 
} DRV8301_GainSetting_e;

typedef enum : uint32_t {
    DRV8301_FaultType_NoFault  = (0 << 0),  //!< No fault

    // Status Register 1
    DRV8301_FaultType_FETLC_OC = (1 << 0),  //!< FET Low side, Phase C Over Current fault
    DRV8301_FaultType_FETHC_OC = (1 << 1),  //!< FET High side, Phase C Over Current fault
    DRV8301_FaultType_FETLB_OC = (1 << 2),  //!< FET Low side, Phase B Over Current fault
    DRV8301_FaultType_FETHB_OC = (1 << 3),  //!< FET High side, Phase B Over Current fault
    DRV8301_FaultType_FETLA_OC = (1 << 4),  //!< FET Low side, Phase A Over Current fault
    DRV8301_FaultType_FETHA_OC = (1 << 5),  //!< FET High side, Phase A Over Current fault
    DRV8301_FaultType_OTW      = (1 << 6),  //!< Over Temperature Warning fault
    DRV8301_FaultType_OTSD     = (1 << 7),  //!< Over Temperature Shut Down fault
    DRV8301_FaultType_PVDD_UV  = (1 << 8),  //!< Power supply Vdd Under Voltage fault
    DRV8301_FaultType_GVDD_UV  = (1 << 9),  //!< DRV8301 Vdd Under Voltage fault
    DRV8301_FaultType_FAULT    = (1 << 10),

    // Status Register 2
    DRV8301_FaultType_GVDD_OV  = (1 << 23)  //!< DRV8301 Vdd Over Voltage fault
} DRV8301_FaultType_e;



class DRV8301_Gate_Driver 
{
    public:
        /** The DC_CAL and OCTW pins are not connected to the MCU on the Odrive 3.5. 
         * I'm assuming they are also not connected on the ODESC4.2 but haven't confirmed this. */
        DRV8301_Gate_Driver(int nCS_gpio, int EN_gpio, int nFAULT_gpio) : nCS_gpio_(nCS_gpio), EN_gpio_(EN_gpio), nFAULT_gpio_(nFAULT_gpio) {}
        
        /** Once the class is declared, only then can we link a new function
         * that calls "declared_drv_class.fault_pin_asserted_isr_callback"
         * as the pin interrupt callback.  @param handle_nFAULT should be set to 
         * this externally declared/defined function that calls "fault_pin_asserted_isr_callback" */
        bool init(DRV8301_GainSetting_e requested_gain,  SPIClass* spi,  void (*handle_nFAULT)() = nullptr);

        void enable(void);
        void disable(void);

        DRV8301_FaultType_e get_error();
        
        /** The function pointer that is passed as
         * parameter "handle_nFAULT" into the DRV8301_Gate_Driver init function
         * should call "fault_pin_asserted_isr_callback." */
        void fault_pin_asserted_isr_callback(void);

        /** "EN_pin_controlled_level" is only what we set the value to,
         * if the enable pin is shorted high or low and is overpowering 
         * the MCU's output drive strength, we do not capture that information. */
        bool EN_pin_controlled_level; 
        bool nFAULT_pin_level;
        bool has_nFAULT_tripped = false;
        uint32_t error_code_when_nFAULT_tripped = DRV8301_FaultType_NoFault;

    private:
        enum CtrlMode_e {
            DRV8301_CtrlMode_Read = 1 << 15,   //!< Read Mode
            DRV8301_CtrlMode_Write = 0 << 15   //!< Write Mode
        };

        enum RegAddr_e {
            kRegAddrStatus1  = 0 << 11,  //!< Status Register 1
            kRegAddrStatus2  = 1 << 11,  //!< Status Register 2
            kRegAddrControl1 = 2 << 11,  //!< Control Register 1
            kRegAddrControl2 = 3 << 11   //!< Control Register 2
        };

        struct RegisterFile {
            uint16_t control_register_1;
            uint16_t control_register_2;
        };

        static inline uint16_t build_ctrl_word(const CtrlMode_e ctrlMode,
                                            const RegAddr_e regName,
                                            const uint16_t data) {
            return ctrlMode | regName | (data & 0x07FF);
        }

        /** @brief Reads data from a DRV8301 register */
        bool read_reg(const RegAddr_e regName, uint16_t* data);

        /** @brief Writes data to a DRV8301 register. There is no check if the write succeeded. */
        bool write_reg(const RegAddr_e regName, const uint16_t data);

        int nCS_gpio_;
        int EN_gpio_;
        int nFAULT_gpio_;

        const int SPI_CLOCK_SPEED_HZ_DRV = 8000000UL;

        SPIClass* spi_class_ptr;

        SPISettings spi_settings; //!< SPI settings variable

        uint16_t tx_buf_, rx_buf_;
};


#endif // __DRV8301_HPP

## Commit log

2025-02-10 DRV8301 Driver updates, untested
    - Fixed bug that always would set a gain value of 10V/V
    - Cleaned up code a little bit
    - Lowered the overcurrent fault threshold of the Vds OC measurements.
    [main.cpp]
2025-02-15 Updated gains to increase current sense resolution
    Behavioral changes of the pendulum make cogging torque visible now that the control is much more sensitive.
2025-02-18 New AS5048 Driver
    -made a new driver specifically for the AS5048A that inherits the simpleFOC's Sensor class like the other MagneticSPI classes, but adds in diagnostics for error flags and diagnostic warnings. The driver needs some cleanup but is good enough for now
    -fixed spi phase setting being incorrect, now we read the full resolution of sensor data
    -increased current gain to 80V/V
    -changed control gains, tuning needs a lot more work
    [ODESC_4p2 Pinout.xlsx]
2025-02-20 Cleanup and bugfixes
    -made the voltage scaling match the power supply voltage (12v vs 20v), control is much better now
    -fixed startup wait time issues for DRV8301 (after driving EN_GATE high) and the mag sensor (3v3 rail power on to SPI message wait time)
    [AS5048A_MagSenseSPI.cpp, main.cpp]
2025-02-23 Driver bugfixes
    [Pendulum Axle to Moment Adapter 6mm shaft version.stl]
2025-02-24 cleanup and add v sense to 3rd adc inj channel
2025-03-01 bugfixes, cleanup, tuning
    -cleaned the code up a little
    -fixed bug in biquad filter class that had wrong polarities for the Bx coefficients
    -improved tuning a lot. It seems the cogging torque and current sensor's signal to noise ratio is limiting the controllability right now. New current shunts were ordered (10mOhm -> 100mOhm)
    [ODESC_4p2 Pinout.xlsx, Pendulum General Notes.xlsx]
2025-03-03 tuning, deadtime, and HW changes
    -updated shunt resistor to 200mOhm which may have been too high. 50mOhm seems like an appropriate sweet spot
    -added check for nFAULT being asserted LOW, but it does not distinguish between EN_GATE causing nFAULT to go low, vs true faults, so there is more work to be done
    -HW change, but I updated the perf-board based breakout of the ODESC pins so I can start developing the LED driver for the RGB led strips via pwm'd dma transfers to GPIO.
    [AS5048A Mag Pinout and Slipring Harness.xlsx, ODESC_4p2 Pinout.xlsx]
2025-03-12 cleanup, tuning and started rgb led driver
    -fixed issue where disabling the gate driver would falsely report that nFAULT was asserted
    [Pendulum General Notes.xlsx]
2025-03-16 WS2812B Driver WIP
    [Pendulum General Notes.xlsx]
2025-03-23 WS2812B Driver Bugfixes, ADC interface WIP
    [ODESC_4p2 Pinout.xlsx]
2025-03-26 ADC Interface and NTC LUT
    [ODESC_4p2 Pinout.xlsx]
2025-04-13 ADC NTC's Interface, RGB LED control WIP, OLED display WIP
    [ODESC_4p2 Pinout.xlsx]
2025-05-08 RGB Wrapper WIP - Untested
    [ODESC_4p2 Pinout.xlsx, Pendulum General Notes.xlsx]
2025-05-13 RGB LED Wrapper/Graphics POC
    [Pendulum General Notes.xlsx]
2025-05-17 OLED Driver Change screen dimensions
    [Pendulum General Notes.xlsx]
2025-05-18 OLED Driver Added ability to rotate display
2025-05-19 Uploaded V1 STEP file, demonstration Gif and photos
    [Assembly.step, Pendulum Axle to Moment Adapter 6mm shaft.step]
2025-05-30 g4 and moteus documentation
    [Moteus x1 Pinout.xlsx, STM32G474CEx GPIO Alternate Function Mapping.csv, moteus_x1_BOM.xlsx]
2025-06-03 Added cmake based blank project for stm32g474CETx
2025-06-07 DMA Bitbang Proof of Concept WIP
2025-06-10 Fucked everything up its my repo i can name commits whatever i wants
    [Pendulum General Notes.xlsx]
2025-07-17 Created GPIO and OS_Tick classes, ported over WS2812B driver for G4 support
    [Moteus x1 Pinout.xlsx]
2025-07-20 GPIO bitbang via DMA tested and confirmed on STM32G4xx
2026-04-21 V2 Progress
    [Adapter_Board.kicad_pcb, Adapter_Board.kicad_sch, Pendulum General Notes V2.xlsx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]
